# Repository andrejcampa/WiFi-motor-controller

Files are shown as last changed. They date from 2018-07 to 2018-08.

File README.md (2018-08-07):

# Wifi motor controller

WiFi motor controller is a highly efficient DC motor controller for creating simple remote controlled toys using a mobile device. The main purpose of the project was to build a simple WiFi controller for N/HO scale trains. However, the motor driver is not limited to trains but can also be efficiently implemented to other simple DIY toys.  The project is divided into three independent and customizable parts: hardware (HW) part, software (SW) part and optional custom 3D printed train. 

Key Specifications:
-	Supply voltage 6-15V (polarity insensitive)
-	Maximum output current 0.5A (BD622OF)/ 1A (BDF6221F)
-	Access point to the device (independent to mobile device system), no external software needed to control the device

 # Contents

- [1. HW Part](#1-hw-part) 
- [2. SW Part](#2-sw-part)
- [3. 3D Printed parts](#3-3d-printed-parts)
- [4. Support](#4-support)

Support via PayPal (https://paypal.me/andrejcampa)

## 1. HW Part

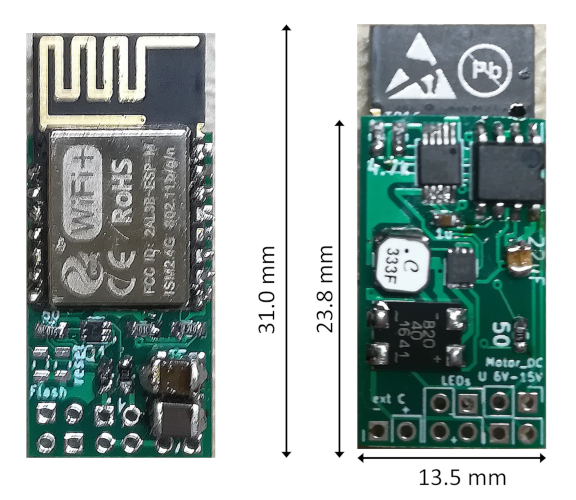
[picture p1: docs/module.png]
module


Fig 1.1: The picture of the front and back of the WiFi motor control with dimensions in mm.

The hardware of the controller was created with KiCad EDA; I have been using nightly builds release 5, since it is a huge step forward with features, libraries, etc. There are some inconsistencies between the Linux and Windows version thus you might need to make some slight changes to the naming of parts (for instance in windows the library symbol for a resistor is device:R while in Linux Device:R).
The hardware is based around BD622XF H-bridge driver and the most important features of HW are summarized in the block diagram. The maximal pulse voltage at the motor is equal to the input voltage reduced by the diode bridge voltage drop (~0.5V). Please consider using the power supply voltage of 12V - 15V to maximize the performance of H-bridge, since the module is very small 13.5 mm x 23.8 mm (31 mm) and the current capacity is limited.

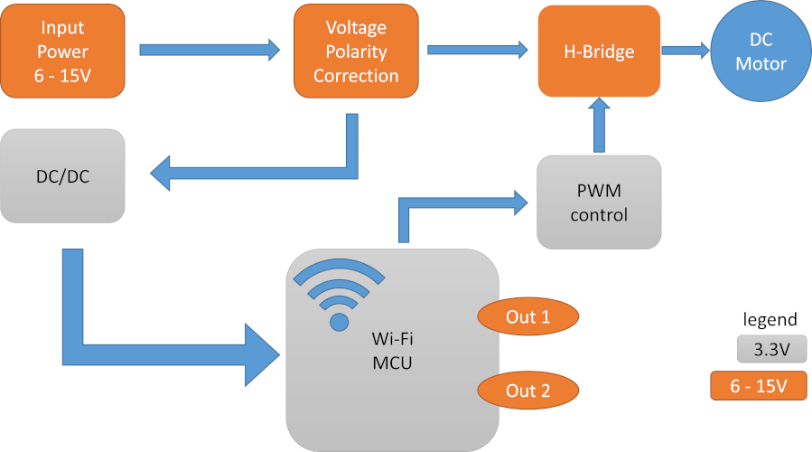
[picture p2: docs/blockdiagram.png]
blockdiagram


Fig. 1.2: Block diagram of the module.

### Interface pins definition and connection

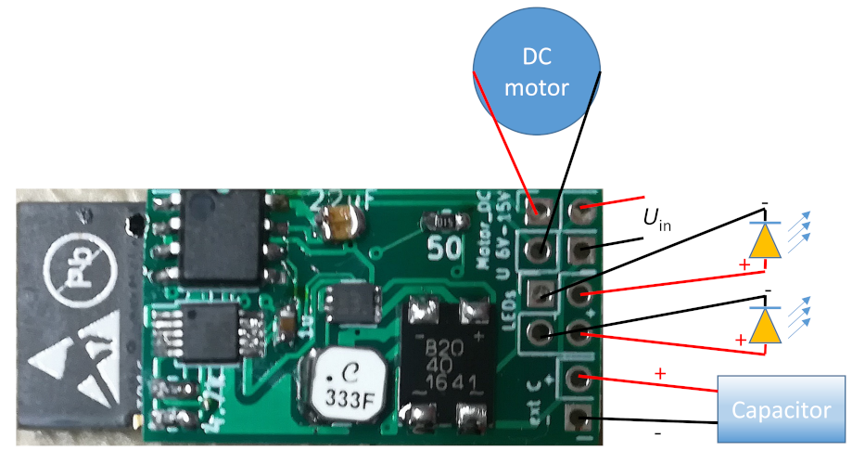
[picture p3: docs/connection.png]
connecting


Fig. 1.3: Definition of pins and “connection scheme”.

Pin name | Description
------------ | -------------
**ext C (- +)** | optional external capacitor, beware of the polarity!
**LEDs** | two connections for LEDs, the maximal current is 10 mA limited by 1k resistor, this is FET driven output connected to high voltage Uin and can be used for signaling. Also marked as out 1 and out 2 in the block diagram.
**Motor_DC** | the output for DC motor, polarity and PWM voltage signal is controlled by MUC.
**U 6V-15V** | main input power for the HW and motor, Uin = 6V-15V

### PCB
The latest Gerber for PCB production can be found in the directory HW/gerber/vlak.zip. The compressed archive was already used and sent to one of the cheap Chinese PCB Manufacturer. Please contact me if you need some additional information or how to reduce the costs of a prototype.

## 2. SW part

### Flashing

The main WiFi + MCU unit is based on a small esp8285 module, ESP-M2 (doit.am). Please refer to documentation how to flash the module. You have the option to program the ESP module on the board. However, you have to supply the power to the input pins and additionally solder the ground, Rx and Tx pin directly to the module (see ESP-M2 documentation).  To flash you will need to short and hold flash pads and in the meantime short the reset pads, Figure 2.1. Flash and Reset pads are exposed on the front side of PCB.

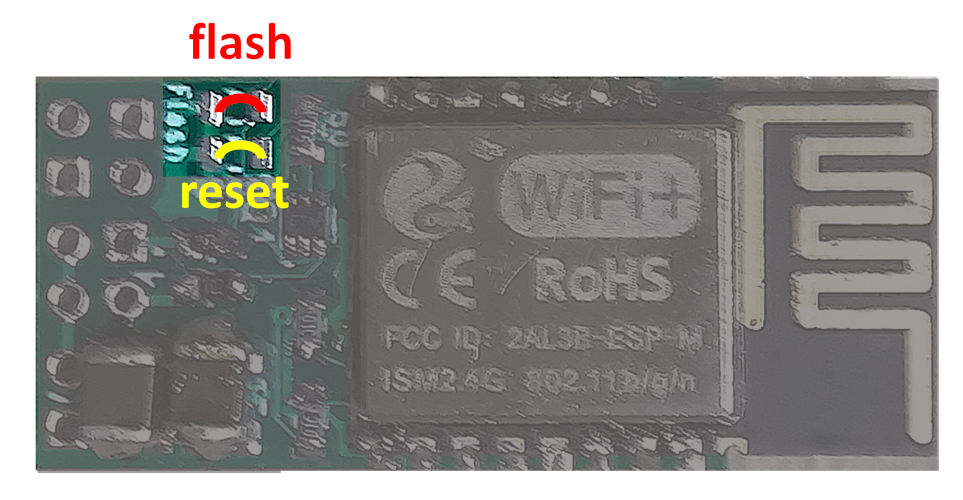
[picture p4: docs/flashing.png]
flashing

Fig. 2.1: Exposed pads for flashing the module.

### Program
The program is written in Arduino IDE, using the open libraries, Arduino core for ESP8266 Wifi chip. To improve the response time I have used an asynchronous web server. The soft access point (SoftAP) is implemented. The program uses for SSID SRS and the serial number (SRS xxxx), the default password is SRS12345 and is for now only changeable from the program. The default page is packed in the header file as the stream of characters (string), so no file system is needed.
To access and to control the module you have to open the web browser after connecting to the hotspot. In the browser you should write the address 192.168.4.1 to access the control panel, Fig 2.2. With the slide bar you can adjust the speed, with the left and right button you can control the direction while the X button will stop the motor. In all cases soft acceleration is adapted to stabilize the module and motor, to have smooth driving experience. On the right side, the two additional buttons for turning LEDs on and off are presented. The program is written for N and HO scale train purposes and can be easily adjusted for other needs by modifying the existing page and program.

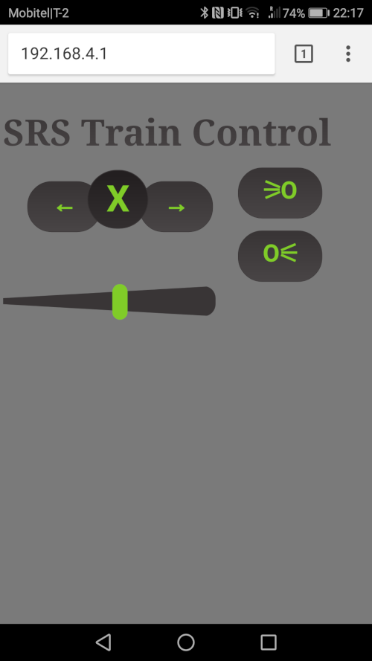
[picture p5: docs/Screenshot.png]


Fig. 2.2: Screenshot of UI.

## 3. 3D printed parts
The first 3-D printed locomotive is in directory 3D. You need FreeCAD to open and edit the locomotive hull. The completed locomotive can be seen in the [demonstration video](https://youtu.be/si7zXm7mwlY).

To use the WiFi module with the 3D printed hull you also need Tomytec TM-07R Motorized Chassis (N scale). By connecting the LEDs (3 mm size) and module like in Fig. 1.3 you should get a connection similar as shown in Fig. 3.1. For this project you can use very thin wires 0.05mm2 (30AWG) since the current capacity of such wire is enough for our 0.5A or 1A maximal current.

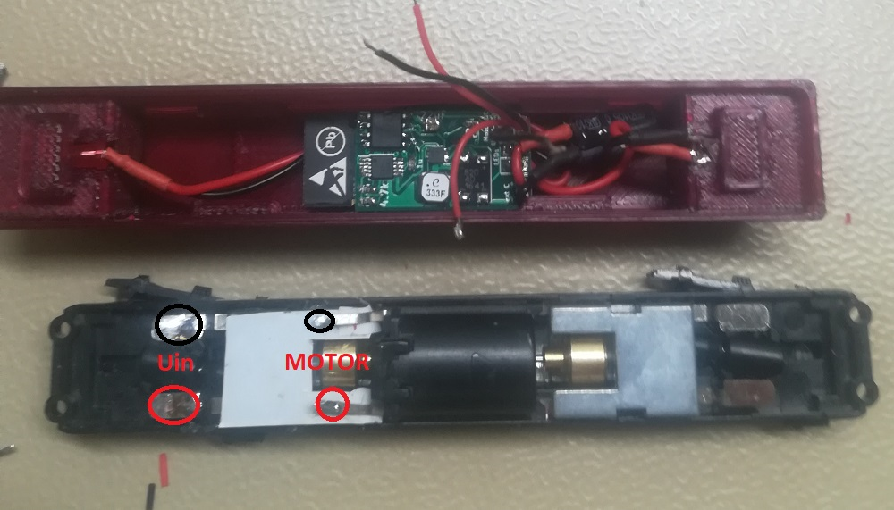
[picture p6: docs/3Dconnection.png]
3D connection


Fig. 3.1: Assembling the module into the 3D printed hull.

Please contact me if the detailed step by step instructions are needed!

## 4. Support
You are encouraged to support the project in many different ways
1. To track bugs.
2. To improve the SW part with a better response.
3. To create custom control panels in HTML.
4. To develop new 3-D printable locomotives on different chassis.
5. To make different toys using the module.
6. ***And last and maybe also very important to support the project by donating the money. The development of the HW part and printable toys take not only the time but also other resources, I have to buy (PCB, electronic components, filament,…). Unfortunately, I have the very limited amount of the own funds for a project, to speed up the development process please think about the donation. With the additional funds, even higher integration could be achieved (especially replacing the ESP module, with custom PCB antenna and ESP8285 SOC).***
7. To reduce the costs of creating a module by yourself we could make a campaign for professional assembly, but the production should be around 100 pieces or more.
8. For testing purposes (very limited amount of pieces) and for the compensation of the costs, I am willing to hand solder a few modules.

Support via PayPal (https://paypal.me/andrejcampa)

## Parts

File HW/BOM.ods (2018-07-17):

regulator | 16V HO/N
 |  | description | link | amount | Price/1 | Price/100
 |  | C 22uf | http://si.farnell.com/murata/grm188r60j226mea0d/cap-mlcc-x5r-22uf-6-3v-0603/dp/2494232?st=0603 22uf | 1 | 0,285 | 0,135
 |  | diode bridge | http://si.farnell.com/bourns/cd-hd2004/diode-bridge-rect-1-ph-40v-smd/dp/2676044 | 1 | 0,587 | 0,394
 |  | C 1uF | http://si.farnell.com/murata/grm188f51c105za01d/cap-mlcc-y5v-1uf-16v-0603/dp/1828849?st=0603 1uf | 1 | 0,0234 | 0,0185
 |  | C 47uf | http://si.farnell.com/murata/grm32ec81c476ke15l/cap-mlcc-x6s-47uf-16v-1210/dp/1907527?st=1210 47uf | 2 | 0,666 | 0,428
 |  | digital potentiometer | http://si.farnell.com/maxim-integrated-products/ds3502u-t-r/digital-pot-10k-single-usop-10/dp/2515903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 | 1 | 1,01 | 0,705
 |  | motor driver | http://si.farnell.com/rohm/bd6220f-e2/h-bridge-driver-18v-0-5a-sop8/dp/1716260?st=bd6220f | 1 | 2,15 | 1,52
 |  | dcdc | http://si.farnell.com/maxim-integrated-products/max15062aata-t/dc-dc-ctrl-sync-buck-500khz-tdfn/dp/2516650RL | 1 | 1,88 | 1,31
 |  | mosfet dual | http://si.farnell.com/vishay/si1026x-t1-ge3/mosfet-n-ch-60v-0-305a-sc-89/dp/2646361?st=n%20mosfet | 1 | 0,35 | 0,247
 |  | inductor 33uH | http://si.farnell.com/coilcraft/lps4018-333mrb/inductor-shld-33uh-20-0-55a-smd/dp/2408110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 | 1 | 0,892 | 0,892
 |  | R 10k | http://si.farnell.com/multicomp/mcwr06x1002ftl/res-thick-film-10k-1-0-1w-0603/dp/2447230?st=10k resistor | 2 | 0,0036 | 0,0021
 |  | R 4.7k | http://si.farnell.com/multicomp/mcwr06x472-jtl/res-thick-film-4k7-5-0-1w-0603/dp/2694880?st=4.7k 0603 resistor | 2 | 0,0034 | 0,002
 |  | R 1k | http://si.farnell.com/multicomp/mcwr06x102-jtl/res-thick-film-1k-5-0-1w-0603/dp/2694685?st=1k 0603 resistor | 2 | 0,0034 | 0,002
 |  | R 50 | http://si.farnell.com/multicomp/mcwr06x49r9ftl/res-thick-film-49r9-1-0-1w-0603/dp/2447381?st=50 0603 resistor | 2 | 0,0036 | 0,0021
 |  | ESP m2 |  | 1 | 1,38 | 1,38
 |  |  | Final price | 19 | 9,9174 | 7,4739
 |  |  | With VAT |  | 12,099228 | 9,118158
 |  | PCB |  |  | 1,84 | 1,84
 |  |  |  |  | 13,939228 | 10,958158

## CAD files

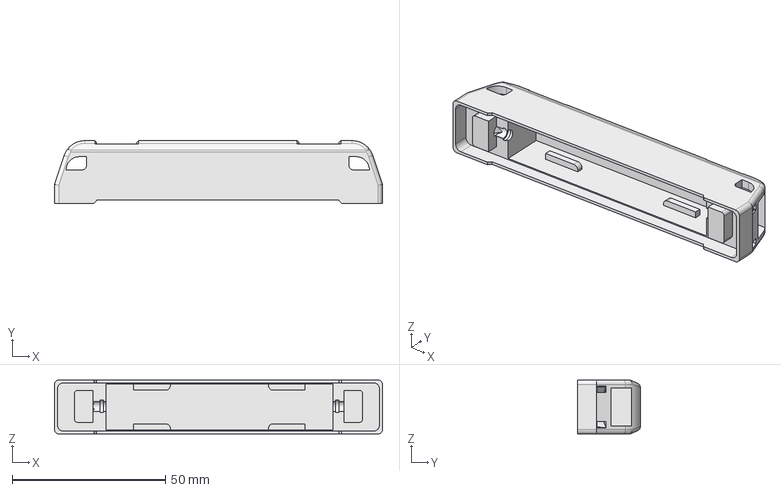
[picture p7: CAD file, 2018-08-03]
3D/train body - like ES64U4.FCStd
107.0 x 20.4 x 17.6 mm

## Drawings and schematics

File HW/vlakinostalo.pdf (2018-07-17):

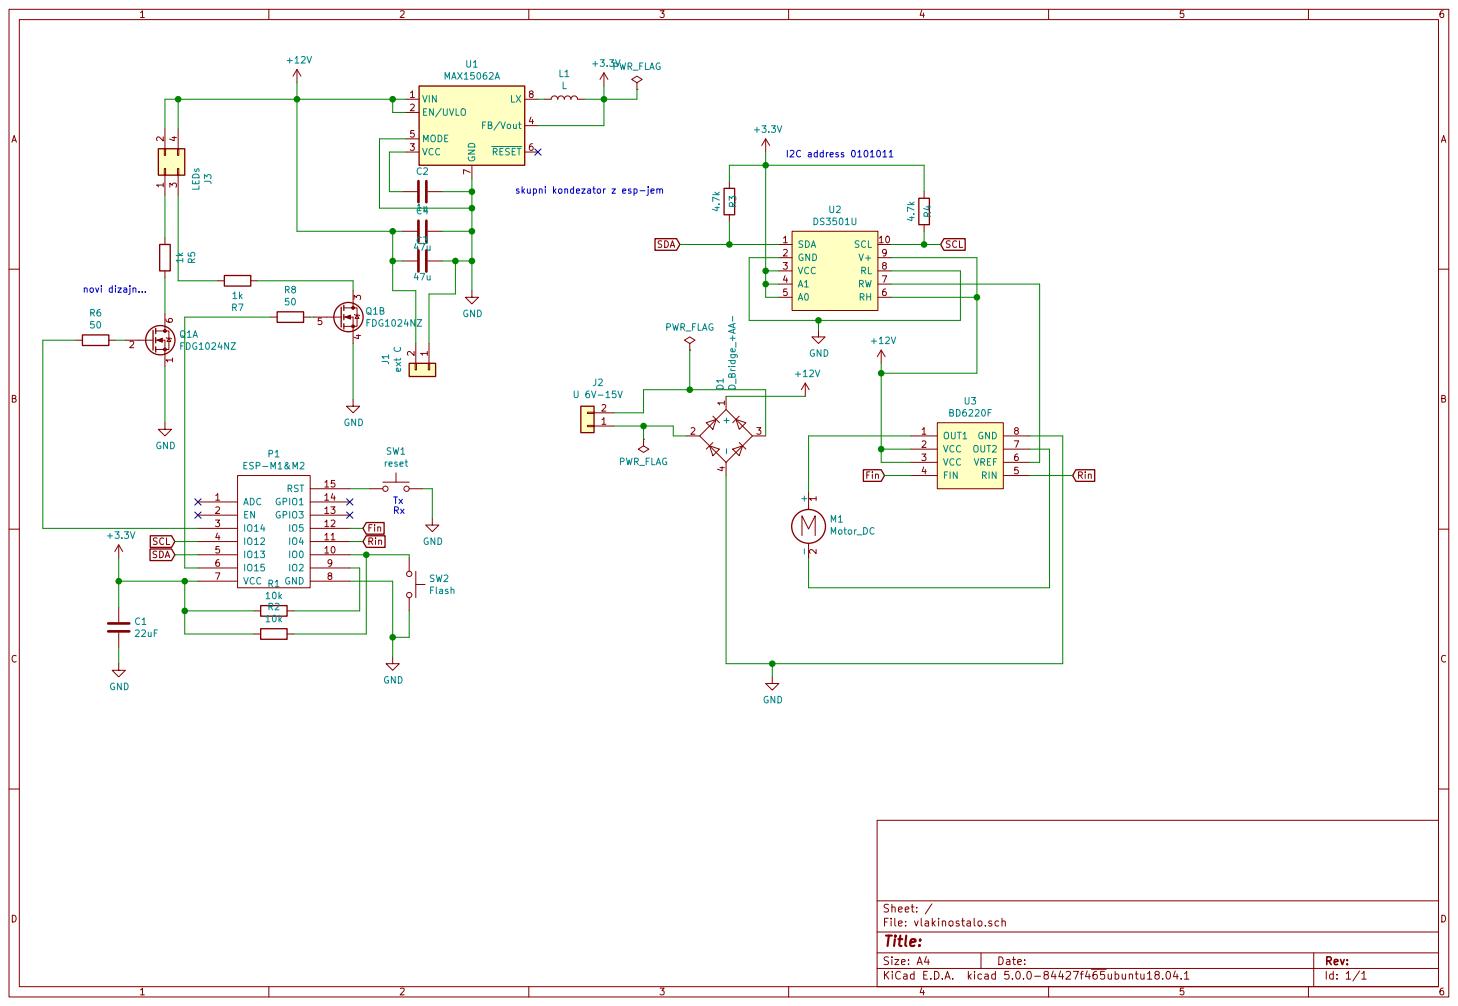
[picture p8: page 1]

skupni kondezator z esp-jem

Id: 1/1 Title: File: vlakinostalo.sch Sheet: / GND

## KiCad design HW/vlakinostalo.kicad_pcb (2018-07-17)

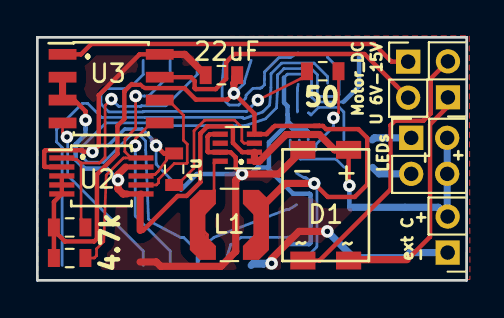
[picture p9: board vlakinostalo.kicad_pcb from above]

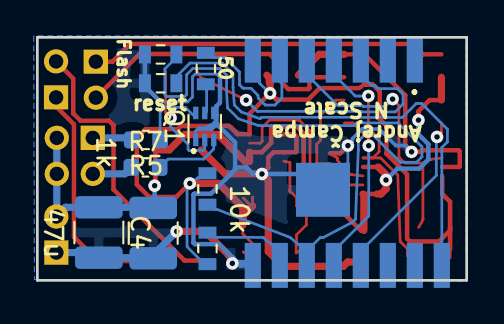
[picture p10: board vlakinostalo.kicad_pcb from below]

Board: 2 copper layers, 23.8 x 13.5 mm, 25 parts (11 on the bottom side), 25 nets.

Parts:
C1: 22uF; C_0603_1608Metric
C2: 1u; C_0603_1608Metric
C3, C4: 47u; C_1210_3225Metric
D1: D_Bridge_+AA-; HD_bridge_bourns
J1: ext C; PinHeader_1x02_P2.00mm_Vertical
J2: U 6V-15V; PinHeader_1x02_P2.00mm_Vertical
J3: LEDs; PinHeader_2x02_P2.00mm_Vertical
L1: L; L_Coilcraft_LPS4018
M1: Motor_DC; PinHeader_1x02_P2.00mm_Vertical
P1: ESP-M1&M2; ESP-M2
Q1: FDG1024NZ; SOT-563
R1, R2: 10k; R_0603_1608Metric
R3, R4: 4.7k; R_0603_1608Metric
R5, R7: 1k; R_0603_1608Metric
R6, R8: 50; R_0603_1608Metric
SW1: reset; R_0603_1608Metric
SW2: Flash; R_0603_1608Metric
U1: MAX15062A; DFN-8_2x2mm_P0.5mm
U2: DS3501U; MSOP-10_3x3mm_P0.5mm
U3: BD6220F; SOIC-8_3.9x4.9mm_P1.27mm

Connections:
+3V3: C1.1, L1.2, P1.7, R1.2, R2.2, R3.1, R4.1, U1.4, U2.3, U2.4, U2.5
+12V: C3.1, C4.1, D1.1, J1.2, J3.2, J3.4, U1.1, U1.2, U2.6, U2.9, U3.2, U3.3
Fin: P1.12, U3.4
GND: C1.2, C2.2, C3.2, C4.2, D1.4, J1.1, P1.8, Q1.1, Q1.4, SW1.2, SW2.2, U1.5, U1.7, U2.2, U2.8, U3.8
unnamed: C2.1, U1.3
unnamed: D1.2, J2.1
unnamed: D1.3, J2.2
unnamed: J3.1, R5.2
unnamed: J3.3, R7.1
unnamed: L1.1, U1.8
unnamed: M1.1, U3.1
unnamed: M1.2, U3.7
unnamed: P1.3, R6.2
unnamed: P1.6, R8.2
unnamed: P1.9, R1.1
unnamed: P1.10, R2.1, SW2.1
unnamed: P1.15, SW1.1
unnamed: Q1.2, R6.1
unnamed: Q1.3, R7.2
unnamed: Q1.5, R8.1
unnamed: Q1.6, R5.1
unnamed: U2.7, U3.6
Rin: P1.11, U3.5
SCL: P1.4, R4.2, U2.10
SDA: P1.5, R3.2, U2.1

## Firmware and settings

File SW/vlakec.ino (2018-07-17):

#include <ESP8266WiFi.h>
#include <WiFiClient.h>
//#include <ESP8266WebServer.h>
#include <ESPAsyncWebServer.h>
#include <Wire.h>
int val=3, val1=3;
int direction=0, direction1=0;
bool sws1=false;
bool sws2=false;
#include "index.h" //Our HTML webpage contents with javascripts
#define forward 5
#define backward 4
#define sw1 14
#define sw2 15



//SSID and Password to your ESP Access Point
const char* ssid = "SRS";
const char* password = "SRS12345";
 
AsyncWebServer server(80);


void setup() {
  Serial.begin(115200);
  WiFi.mode(WIFI_AP);           //Only Access point
  WiFi.softAP(ssid, password);  //Start HOTspot removing password will disable security
  WiFi.persistent(false);
 
  IPAddress myIP = WiFi.softAPIP(); //Get IP address
  Serial.print("HotSpt IP:");
  Serial.println(myIP);
 
server.on("/", HTTP_GET, [](AsyncWebServerRequest *request){
 
    int paramsNr = request->params();

 if (paramsNr){
    for(int i=0;i<paramsNr;i++){
         
        AsyncWebParameter* p = request->getParam(i);
        if (p->name()=="direction"){
          direction1=p->value().toInt();
      
        }
        else if(p->name()=="speed"){ //spremenimo hitrost
          val1=p->value().toInt();
      
        }
        else if(p->name()=="sw"){ //spreminjamo osvetlitev
          int sw=p->value().toInt();
          if (sw==1){
            sws1=!sws1;
            digitalWrite(sw1, sws1);  
            }
          else {
            sws2=!sws2;
            digitalWrite(sw2, sws2);  
            }
        }

    }
 }
  else{   // če ni paramtera pošljemo stran
    request->send(200, "text/html", MAIN_page); //če ni nič od zgoraj pošljemo stran
  }
  });
  
  server.begin();                  //Start server
  Serial.println("HTTP server started");
  

  pinMode(forward, OUTPUT); //forward
  pinMode(backward, OUTPUT); //reverse
  pinMode(sw1, OUTPUT); //switch 1
  pinMode(sw2, OUTPUT); //switch 2
  Wire.begin(13,12); //Wire.begin([SDA], [SCL]).
  Wire.beginTransmission(B0101011); //potentiometer 0...127
  int    error = Wire.endTransmission();
  
  //posljemo vrednost
  Wire.beginTransmission(B0101011);
  Wire.write(byte(0x00));            // sends instruction byte
  Wire.write(byte(val));             // sends potentiometer value byte
  Wire.endTransmission(); 
}



// the loop function runs over and over again forever
void loop() {


//če smo počasni spremenimo smer

if (val<20){
  if (direction1!=direction) {
      
      if (direction1==-1){
        digitalWrite(forward, LOW);   
        digitalWrite(backward, HIGH); 
        //Serial.print("direction -1\n");
      }
      else if (direction1==1){
        digitalWrite(forward, HIGH);   
        digitalWrite(backward, LOW);
        //Serial.print("direction 1\n"); 
      }
      else if (direction1==0){
        digitalWrite(forward, LOW);   
        digitalWrite(backward, LOW);
        //Serial.print("direction 0\n");
      }
   direction=direction1;
   }  
  
  }
    if (direction1!=direction){
        val--;
        Wire.beginTransmission(B0101011);
        Wire.write(byte(0x00));            // sends instruction byte
        Wire.write(byte(val));             // sends potentiometer value byte
        Wire.endTransmission();
        //Serial.print("nizam, direction!\n");
        delay(5); 
      } 
    else if(direction1==direction){
      if (val>val1){
        val--;
        Wire.beginTransmission(B0101011);
        Wire.write(byte(0x00));            // sends instruction byte
        Wire.write(byte(val));             // sends potentiometer value byte
        Wire.endTransmission();
        //Serial.print("nizam hitrost\n");
        delay(5); 
        }
      else if (val1>val) {
      val++;
        Wire.beginTransmission(B0101011);
        Wire.write(byte(0x00));            // sends instruction byte
        Wire.write(byte(val));             // sends potentiometer value byte
        Wire.endTransmission();
        //Serial.print("visam hitrost!\n");
        delay(5); 
      }
     } 
    

}

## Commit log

2018-07-17 Initial HW commit
    [BOM.ods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]
2018-08-03 first 3D printed body
    3D printable body for Tomytec TM-07R Motorized Chassis.
    [train body - like ES64U4.FCStd]
